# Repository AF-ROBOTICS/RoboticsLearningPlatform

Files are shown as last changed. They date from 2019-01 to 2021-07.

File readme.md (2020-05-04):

# DFEC Robot

The DFEC Robot was created for the Department of Electrical and Computer Engineering (ECE) at the US Air Force Academy. It is used to teach ECE fundamentals in the major's introductory course. The robot's chassis is built using 3D printed parts. An Arduino Uno Rev3 microcontroller board and a custom designed power and motor controller Printed Circuit Board (PCB) are used to control the robot.

## Labs

Six labs guide the students from soldering the PCB and assembling the robot to using distance and line sensors to guide the robot through a maze.

[Robot PCB](Labs/0_robot_pcb/robot_pcb.pdf) - This lab guides students to solder and test their PCB.

[Robot Build](Labs/1_robot_build/robot_build.pdf) - This lab provides instructions to assemble the robot.

[Robot Motors](Labs/2_robot_motors/robot_motors.pdf) - This lab investigates how the Arduino uses Pulse Width Modulation to drive the robot's motors.

[Robot Drive](Labs/3_robot_drive/robot_drive.pdf) - This lab has students control the motors to drive in specified patterns.

[Robot Line Following](Labs/4_robot_linefollowing/robot_linefollowing.pdf) - This lab integrates the Pololu QTR-8RC Line Sensor Array to enable the robot to follow a black line.

[Robot Wall Following](Labs/5_robot_wallfollowing/robot_wallfollowing.pdf) - This lab integrates the Sharp GP2Y051SK0F 2-15 cm Analog Distance Sensor to enable the robot to follow walls.

[Robot Maze](Labs/6_robot_maze/robot_maze.pdf) - This lab is broken up into three parts: 1) follow a line through a maze; 2) follow a line through a maze and turn around and return to the start of the maze; and 3) navigate a walled maze towards a goal location.

## Libraries

There are two custom libraries used to control the robot. These libraries should be copied into library folder at `root/Documents/Arduino/libraries`.

[Motor](Labs/libraries/Motor/Motor.h) - This library provides functions to drive the robot using left and right PWM values (e.g., `Motor_Init()`, `Motor_Forward(int leftDuty, int rightDuty)`, and `Motor_Stop()`)

[QTR-8RC](Labs/libraries/QTR-8RC/QTR-8RC.h) - This library is adapted from the QTRSensors library to utilize the QTR-8RC Reflectance Sensor Array to determine how far the robot is off a line.

## Projects

There are several projects that incorporate the DFEC Robot into different systems. All of these are works in progress and need to be updated to utilize the new libraries.

## Hardware

### 3D Printed Chassis

Frame developed using [AutoDesk Fusion 360](https://www.autodesk.com/products/fusion-360/overview) and printed on a LulzBot Taz 6.

#### [Base layer](3D_Printing/stl/BaseLayer1.stl)

| Top | Bottom |
| :---: | :---: |
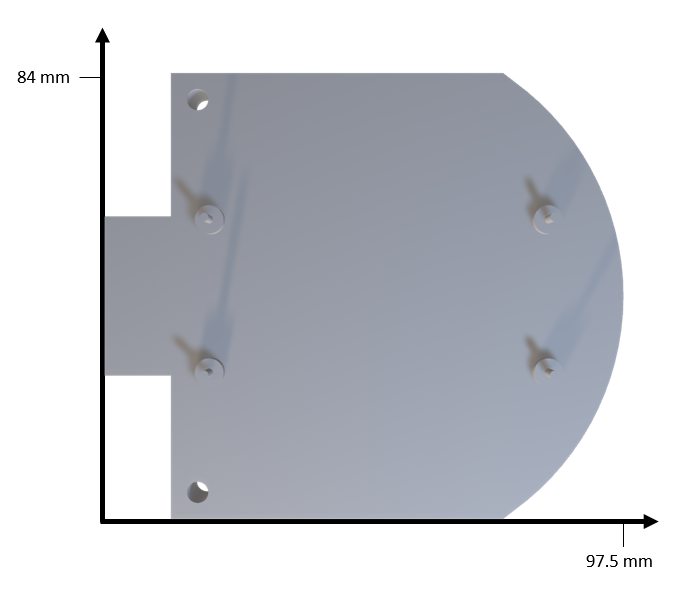
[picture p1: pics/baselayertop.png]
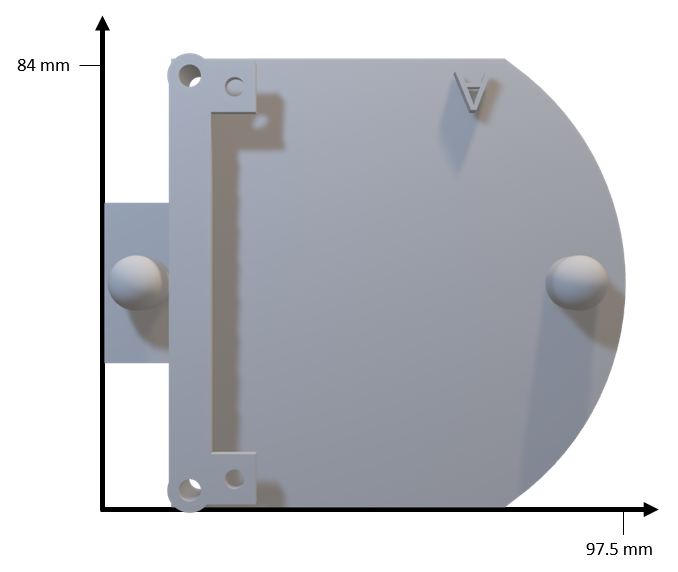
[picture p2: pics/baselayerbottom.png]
|  |  |

#### [Motor layer](3D_Printing/stl/MotorLayer1.stl)

| Top | Bottom |
| :---: | :---: |
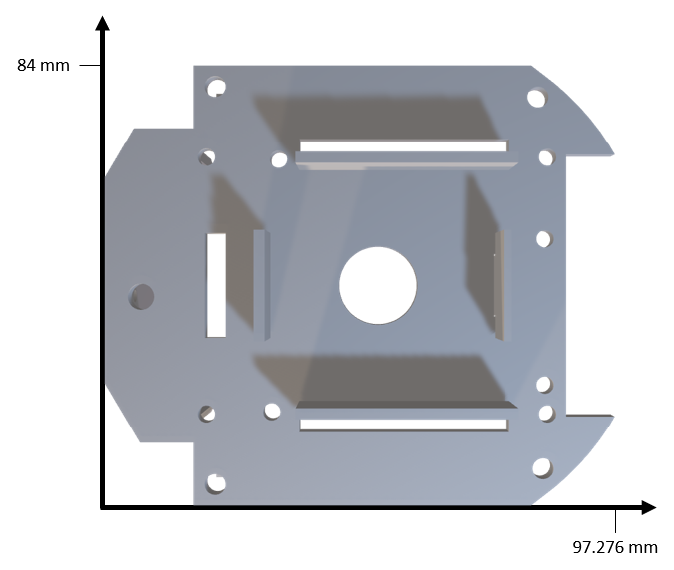
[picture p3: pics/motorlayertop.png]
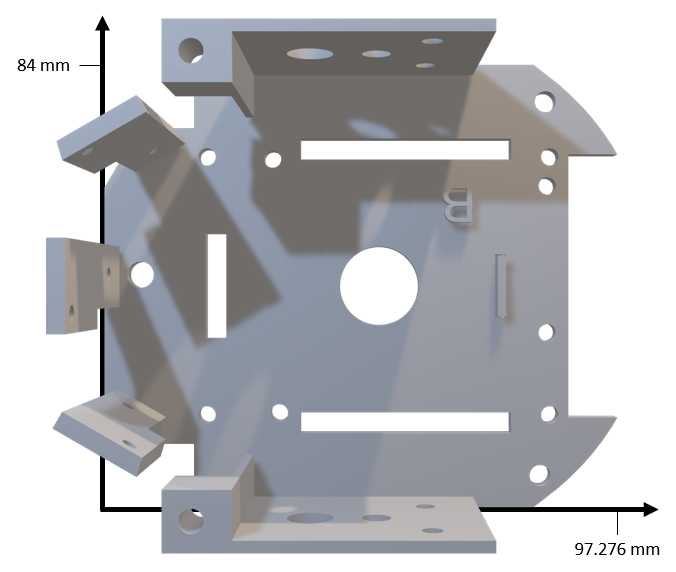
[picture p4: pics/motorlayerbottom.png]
|  |  |

#### [Arduino layer](3D_Printing/stl/ArduinoLayer.stl)

| Top | Bottom |
| :---: | :---: |
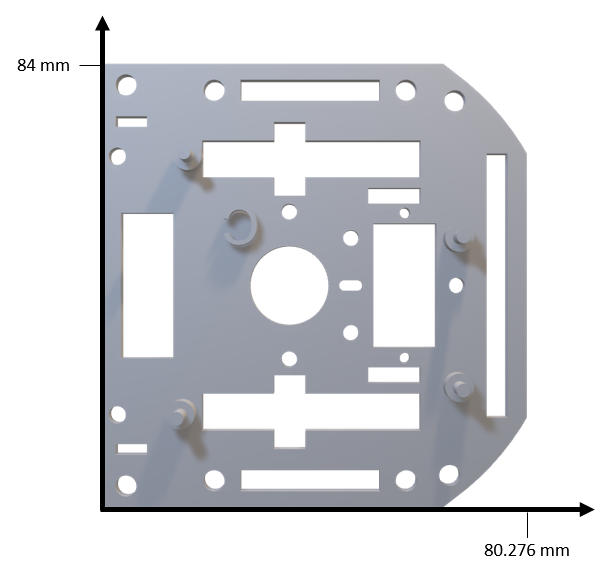
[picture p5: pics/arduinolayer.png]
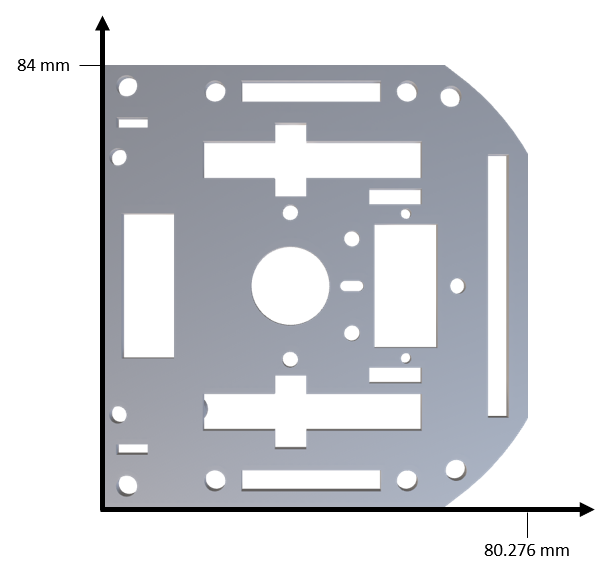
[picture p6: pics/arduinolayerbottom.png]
|  |  |

#### [Additional Layer](3D_Printing/stl/Layer.stl)

| Top | Bottom |
| :---: | :---: |
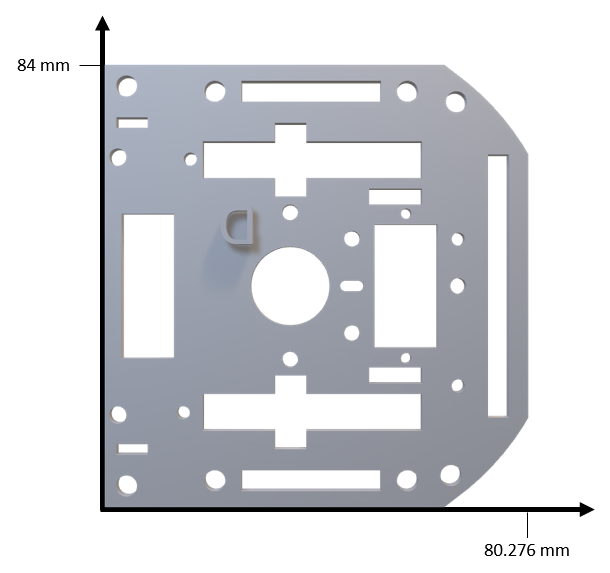
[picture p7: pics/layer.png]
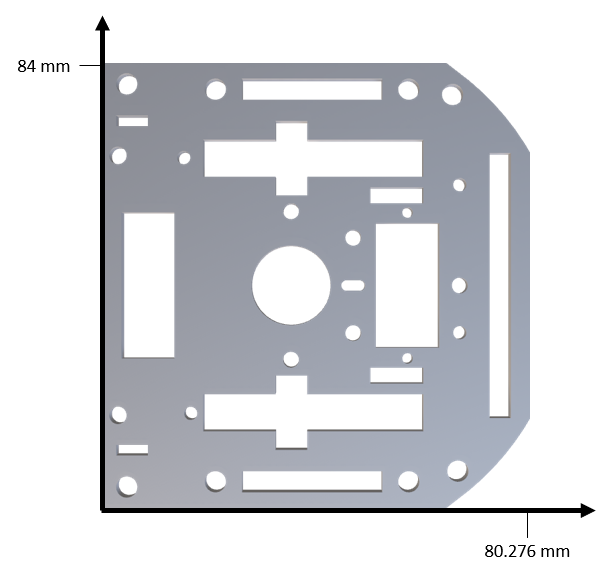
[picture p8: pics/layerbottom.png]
|  |  |

#### Wheels

| [Rims](3D_Printing/stl/rim.STL) | [Tires](3D_Printing/stl/Ninja_Flex_Tire_left.STL) |
| :---: | :---: |
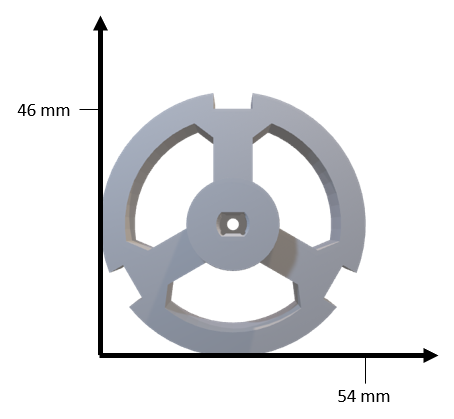
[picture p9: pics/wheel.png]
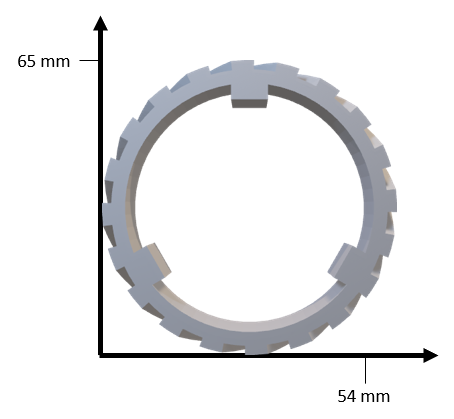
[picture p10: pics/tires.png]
|  |   |

### Printed Circuit Board (PCB)

| | |
| :---: | :---: |
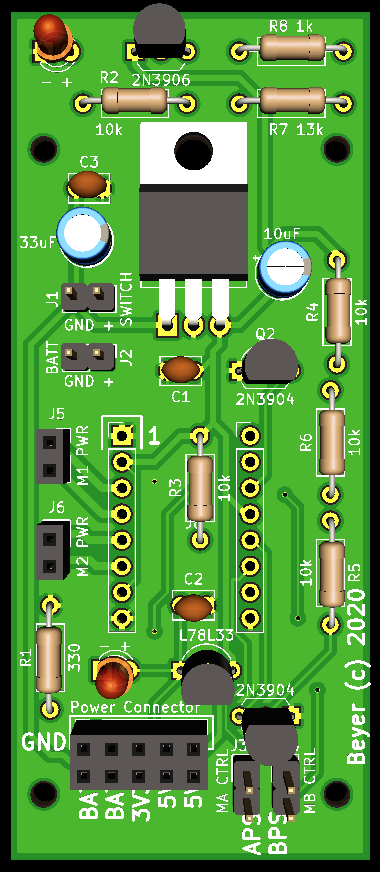
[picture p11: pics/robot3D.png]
|  |  |

### [Motor](https://www.adafruit.com/product/3777)

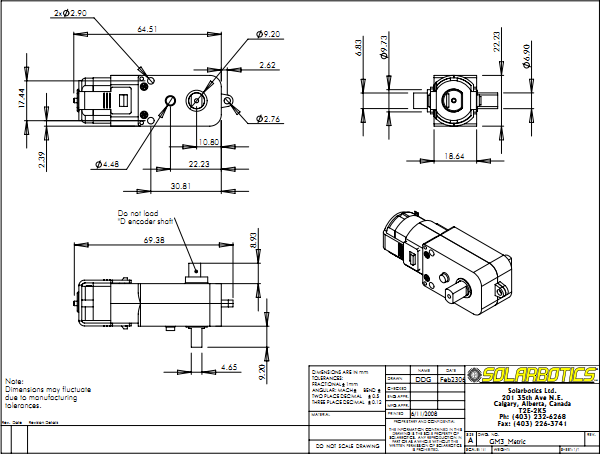
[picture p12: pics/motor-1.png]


### [Sharp GP2Y0A51SK0F Analog Distance Sensor 2-15 cm](https://www.pololu.com/product/2450)

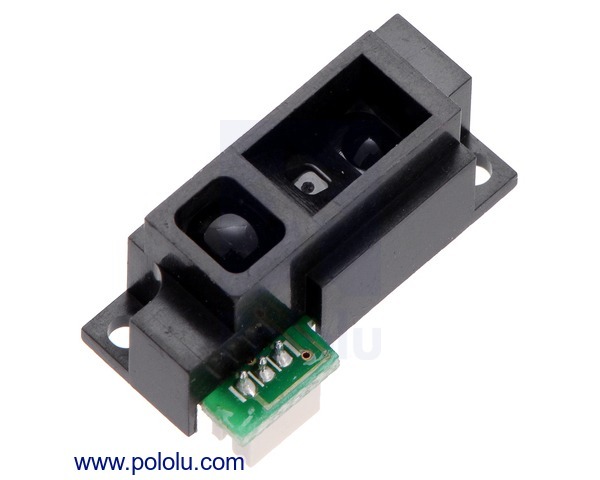
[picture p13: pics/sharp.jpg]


### [QTR-8RC Reflectance Sensor Array](https://www.pololu.com/product/961)

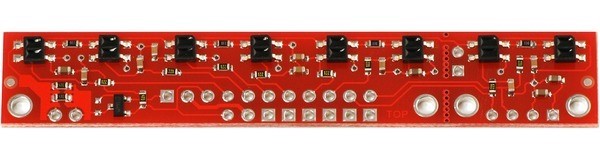
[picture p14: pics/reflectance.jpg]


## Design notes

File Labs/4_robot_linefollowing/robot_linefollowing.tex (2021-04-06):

\documentclass{handout}

%\SetInstructor{Capt Steven Beyer}
\SetCourseTitle{ECE210: Introduction to Electrical and Computer Engineering}
\SetHandoutTitle{Robot Line Following}

%\ShowAllBlanks

\usepackage[obeyspaces]{url}
\input{../arduinoLanguage.tex}

\graphicspath{{./figs/}}

%\showsoln \setsolncolor{red}

\lstset { %
	language=Arduino,
	frame=none,
	basicstyle=\footnotesize,
}

\begin{document}
	\maketitle
		\begin{figure}[H]
		\centering
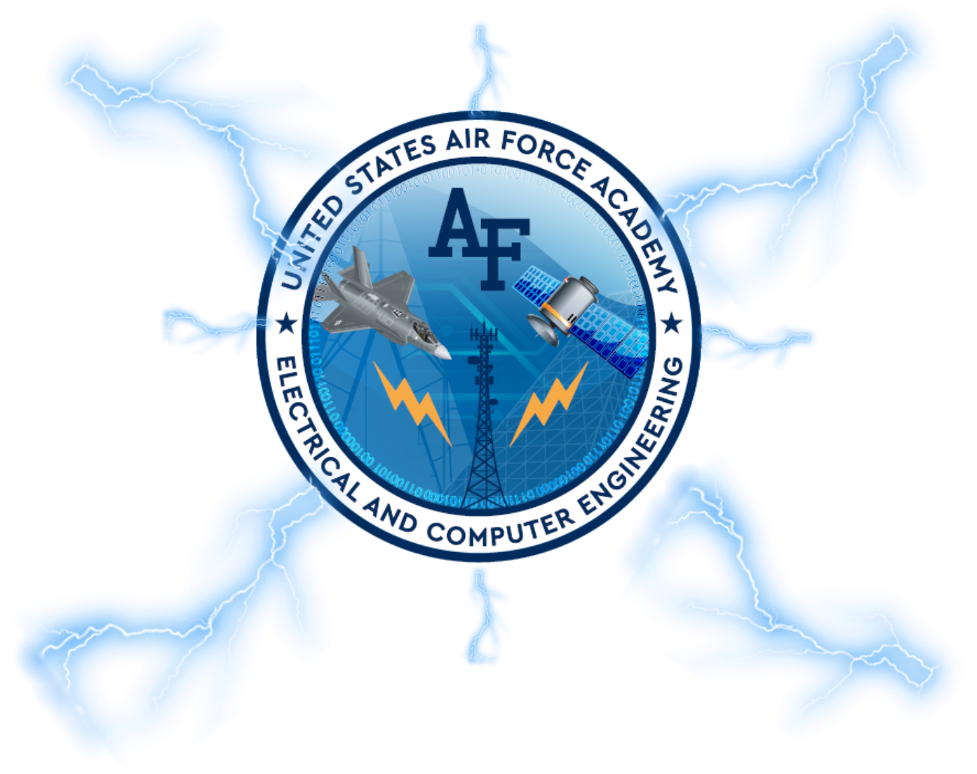
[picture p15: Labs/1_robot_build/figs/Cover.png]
		
	\end{figure}
	
	\section{Objectives.} 
	\begin{enumerate}
		\item Become familiar with the QTR-8RC Line Sensor Array.
		\item Utilize the Arduino to detect lines.
		\item Integrate the Line Sensors with the DFECBot and program the DFECBot to follow a line.
	\end{enumerate}
	
	\section{Materials.}
	\begin{enumerate}
		\item 1x QTR-8RC Reflectance Sensor Array
		\item DFECBot
		\item USB Programming Cable
		\item Black Tape
	\end{enumerate}
	
	\section{Introduction.}
	
	\subsection{QTR-8RC Reflectance Sensor Array}
	The QTR-8RC Line Sensor Array uses 8 infrared radiation (IR) reflectance sensor with an IR light-emitting diode (LED) and an IR sensitive phototransistor.\footnote{Information found at Pololu, \url{https://www.pololu.com/product/961}} The sensors are powered using the $3.3\ V$ and ground pins on the Arduino. Powering the sensors illuminates the IR LED. A $100\ \Omega$ resistor is on-board and placed in series with the LED to limit current. The output of the phototransistor is tied to a $10\ nF$ capacitor. The faster the capacitor discharges, the more reflective the surface is.\footnotemark[1] The QTR sensors have an optimal sensing distance of $3\ mm$.
	
	Wire your QTR-8RC Reflectance Sensor Array to the Arduino according to the schematic shown in Figure~\ref{Fig Line}.
	
	\begin{figure} [H]
		\centering
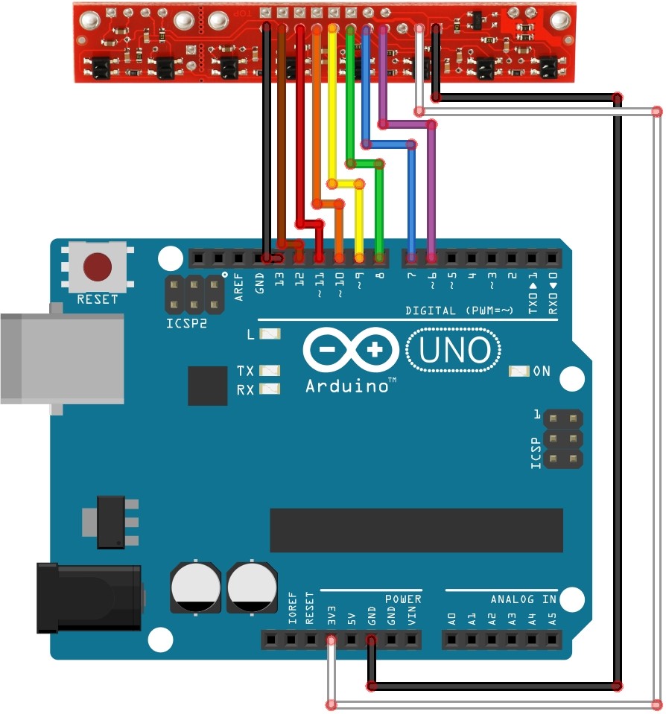
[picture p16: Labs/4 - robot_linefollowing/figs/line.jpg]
		
		\caption{QTR-8RC Reflectance Sensor Array Wiring Schematic}
		\label{Fig Line}
	\end{figure}
	
	\subsection{Example Code}
	Copy the Arduino sketch folder \path{robot_linefollowing}  from \textbf{Teams} (\path{Labs/robot_linefollowing}). Copy the \path{QTR-8RC} library from \textbf{Teams} (\path{Labs/Custom Libraries/QTR-8RC}) to your documents folder: \path{Documents/Arduino/libraries/}. Open the \path{robot_wallfollowing.ino} sketch.
	
	\subsection{QTR-8RC.h}
	The Arduino Sketch utilizes a library called QTR-8RC. This is a custom library adapted from the QTRSensors library to utilize the QTR-8RC Reflectance Sensor Array. This library provides functions to read values from the sensor array and return the distance off the line.
	
	\subsubsection{robot\_linefollowing.ino}
	This example Arduino Sketch provides code to calibrate the DFECBot's QTR-8RC Reflectance Sensor Array and determine the distance off a black line.
	
	\begin{lstlisting}
  // read calibrated sensor values and obtain a measure of the line position
  // with a position of 0.1 mm relative to the center of the line 
  // -33.2 mm to 33.2 mm
  int16_t position = qtr.readLineBlack(sensorValues);
	\end{lstlisting}
	
	\section{Procedure}
	\textbf{Use the example code provided, \path{robot_linefollowing}, \path{Motor.h}, and \path{QTR-8RC.h} to code the DFECBot to do the following:}
		
	\begin{enumerate}
		\item Use a ruler to confirm the accuracy of the line sensor read function
		\item Program the DFECBot to follow a line
	\end{enumerate}
	{\large \textbf{\underline{CALIBRATION:}}} The first 10 seconds after powering on your robot (or uploading the code) is used to calibrate your line sensor. During calibration, \textbf{without lifting your robot off the surface}, slowly move your robot so each line sensor is over a black line for approximately one second. This allows the script to collect minimum (white surface) and maximum (black surface) readings used to calibrate the sensors.
	
	{\large \textbf{\underline{HINT:}}} You should remove all print statements and delays when testing your line following.
	\section{Notes on Proportional Controller:}
\end{document}

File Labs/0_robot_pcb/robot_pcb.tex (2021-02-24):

\documentclass{handout}

%\SetInstructor{Capt Steven Beyer}
\SetCourseTitle{ECE210: Introduction to Electrical and Computer Engineering}
\SetHandoutTitle{Robot PCB}

%\ShowAllBlanks

\usepackage[obeyspaces]{url}

\graphicspath{{./figs/}}

%\showsoln \setsolncolor{red}

\begin{document}
	%	\footnotetext{Examples are abstracted from Tutorials Point, "Arduino", 2019, accessed Feb 18, 2019. [Online]. Available: https://www.tutorialspoint.com/arduino/index.htm}
	\maketitle
	
	\begin{figure}[H]
		\centering
		
	\end{figure}
	
	\section{Objectives.} 
	\begin{enumerate}
		\item Demonstrate the ability to build a robotics system using Electrical and Computer Engineering (ECE) fundamentals such as soldering, assembly, and fabrication.
		\item Troubleshoot ECE applications utilizing modern test equipment.
	\end{enumerate}
	
	\section{Materials.}
\begin{minipage}{.5\textwidth}
	\begin{enumerate}
		\item Printed Circuit Board (PCB)
		\item 1 - $330\ \Omega$ resistor (R1)
		\item 5 - $10\ k\Omega$ resistors (R2 - R6)
		\item 1 - $13\ k\Omega$ resistor (R7)
		\item 1 - $1\ k\Omega$ resistor (R8)
		\item 3 - $0.1\ \mu F$ ceramic disc capacitors (C1-C3)
		\item 1 - $10\ \mu F$ radial capacitor (C4)
		\item 1 - $33\ \mu F$ radial capacitor (C5)
		\item 2 - 2N3904 transistors (Q1-Q2)
		\item 1 - 2N3906 transistor (Q3)
	\end{enumerate}
\end{minipage}\hfill
\begin{minipage}{.5\textwidth}
	\begin{enumerate}\setcounter{enumi}{10}
		\item 1 - L7805 $5\ V$ voltage regulator (U1)
		\item 1 - L78L33 $3.3\ V$ voltage regulator (U2)
		\item 2 - red LEDs
		\item Headers
		\begin{enumerate}
			\item 4 - 1x2 male headers (J1-J4)
			\item 2 - 1x2 female headers (J5 and J6)
			\item 1 - 2x5 female header (Power Connector)
			\item 2 - 8x1 female headers (Motor Driver)
		\end{enumerate}
		\item Motor Driver
		\begin{enumerate}
			\item Motor Driver Board
			\item 2 - 8x1 male headers
		\end{enumerate}
	\end{enumerate}
\end{minipage}

\newpage
\clearpage
\pagebreak
	
	\section{PCB}
	Your PCB should look like the below figure with all components labeled. This PCB provides power and motor functionality for your robot.
		\begin{figure} [H]
			\centering
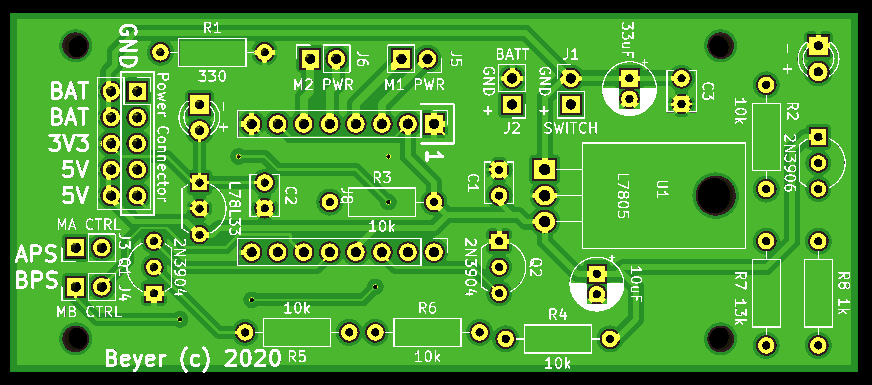
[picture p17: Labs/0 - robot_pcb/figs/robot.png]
			
			\caption{Printed Circuit Board}
		\end{figure}

	\section{Resistors}
	Gather the 8 resistors. Confirm actual resistance using the digital multimeter (DMM). These are non-directional. Solder each onto the board.
	
	\begin{figure} [H]
		\centering
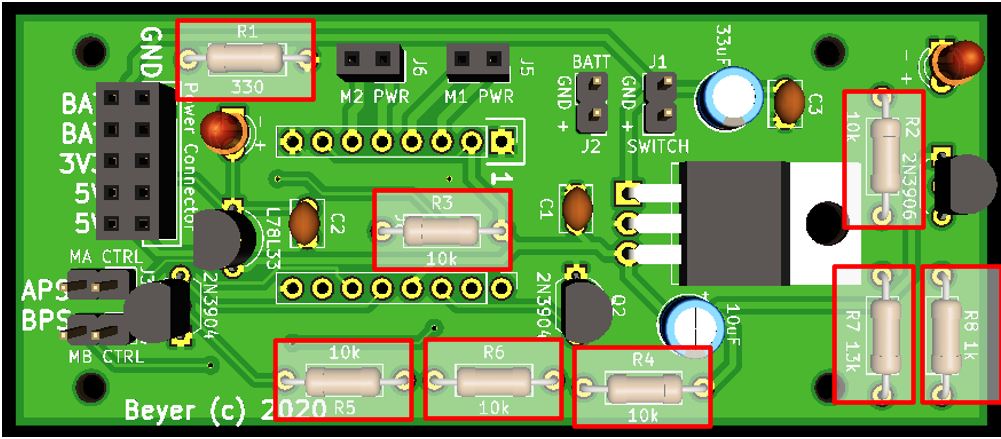
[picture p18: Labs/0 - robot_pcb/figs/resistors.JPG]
		
		\caption{Resistors}
	\end{figure}
	
	\section{Ceramic Disc Capacitors}
	Gather the 3 ceramic disc capacitors. These are non-directional. Solder each onto the board.
	
	\begin{figure} [H]
		\centering
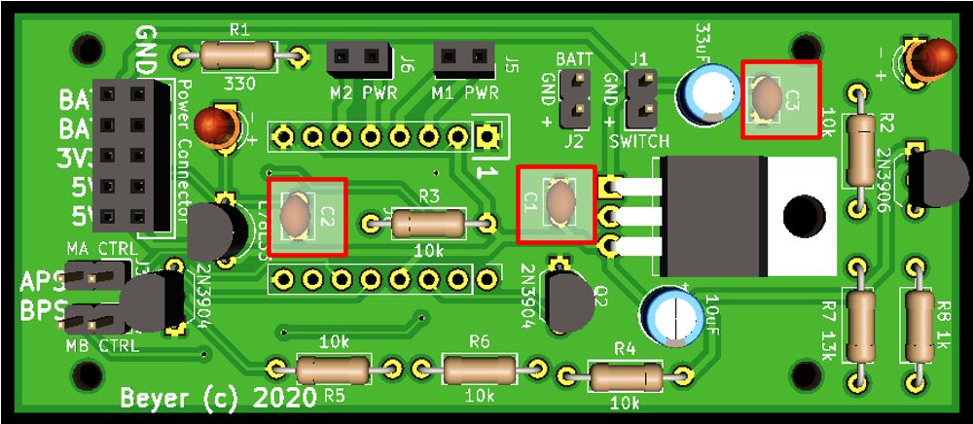
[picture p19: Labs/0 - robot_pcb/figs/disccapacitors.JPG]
		
		\caption{Ceramic Disc Capacitors}
	\end{figure}
	
	\newpage
	\clearpage
	\pagebreak
	
	\section{Radial Capacitors}
	Gather the 2 radial capacitors. These are directional. The negative sign on the capacitor cap should be oriented opposite the positive on the board. Solder each onto the board.
	
	\begin{figure} [H]
	\centering
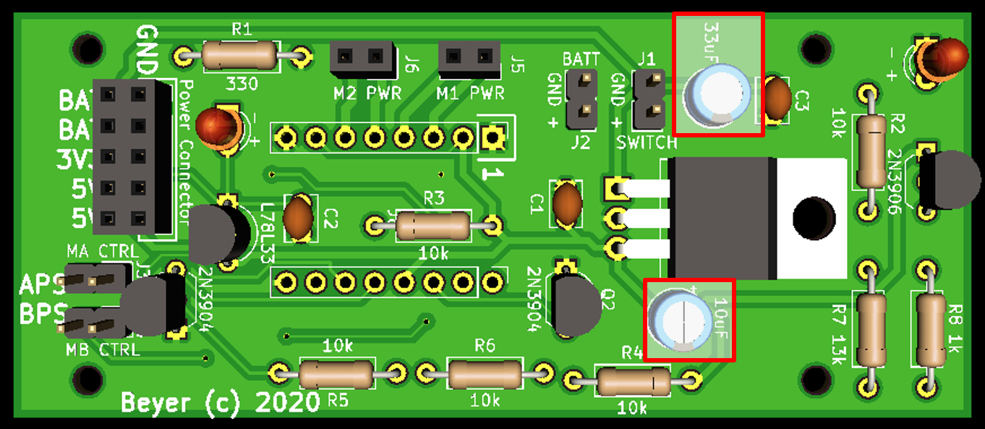
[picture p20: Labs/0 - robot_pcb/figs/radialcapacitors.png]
	
	\caption{Radial Capacitors}
	\end{figure}

	\section{Transistors}
	Gather the 3 transistors. These are directional. The flat edge of the transistor should correspond with the board. Solder each onto the board.
	
	\begin{figure} [H]
		\centering
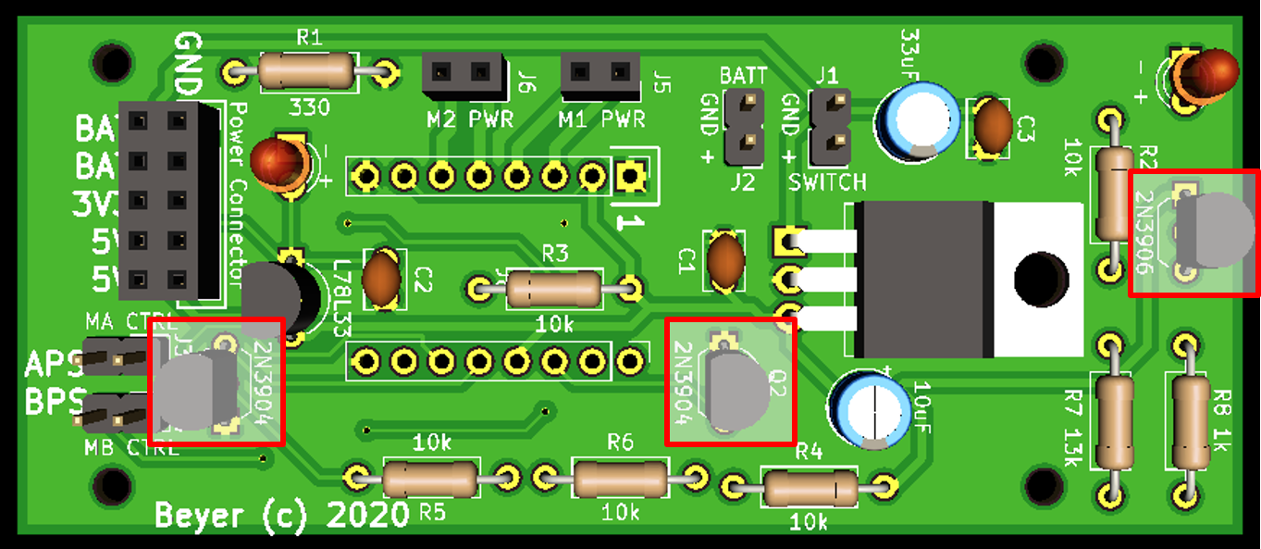
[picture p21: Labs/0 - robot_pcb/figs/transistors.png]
		
		\caption{Transistors}
	\end{figure}
	
	\section{5 V Voltage Regulator}
	Gather the $5\ V$ voltage regulator. Use pliers to bend the leads $90^o$ towards the back of the regulator (flat side) at the point that the lead thins. Place the regulator so that the flat side lays flat on the top of the PCB. Solder it onto the board.
	
	\begin{figure} [H]
		\centering
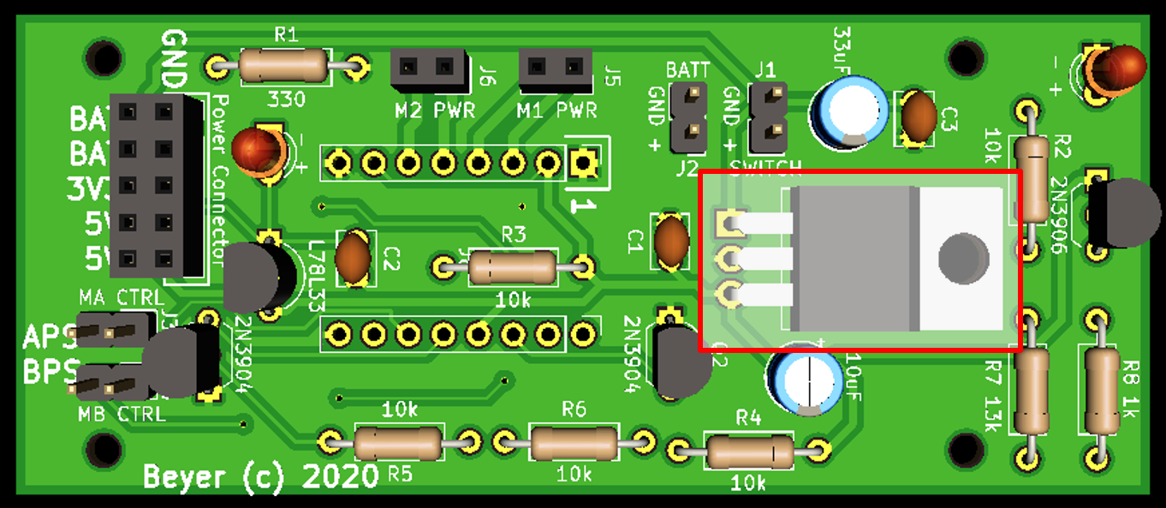
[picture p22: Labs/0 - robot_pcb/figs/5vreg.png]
		
		\caption{$5\ V$ Voltage Regulator}
	\end{figure}

\newpage
\clearpage
\pagebreak

	\section{3.3 V Voltage Regulator}
	Gather the $3.3\ V$ voltage regulator. This is directional. The flat edge of the regulator should correspond with the board. Solder it onto the board.
	
	\begin{figure} [H]
		\centering
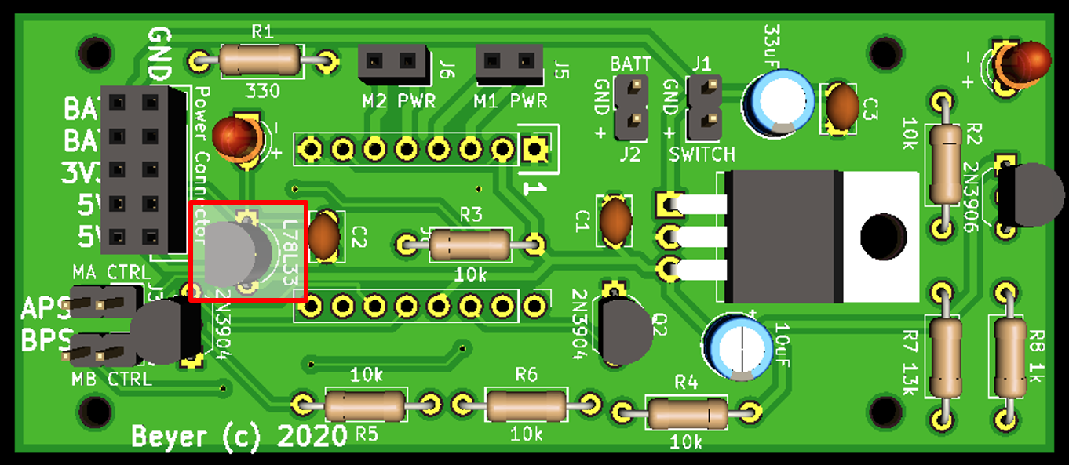
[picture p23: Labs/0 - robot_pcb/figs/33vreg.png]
		
		\caption{$3.3\ V$ Voltage Regulator}
	\end{figure}
	
	\section{LEDs}
	Gather the 2 LEDs. Use the DMM to make sure both are operational. These are directional. The \textbf{flat} edge of the LED and the \textbf{short} lead should be oriented toward the negative on the board. Solder them onto the board.
	
	\begin{figure} [H]
		\centering
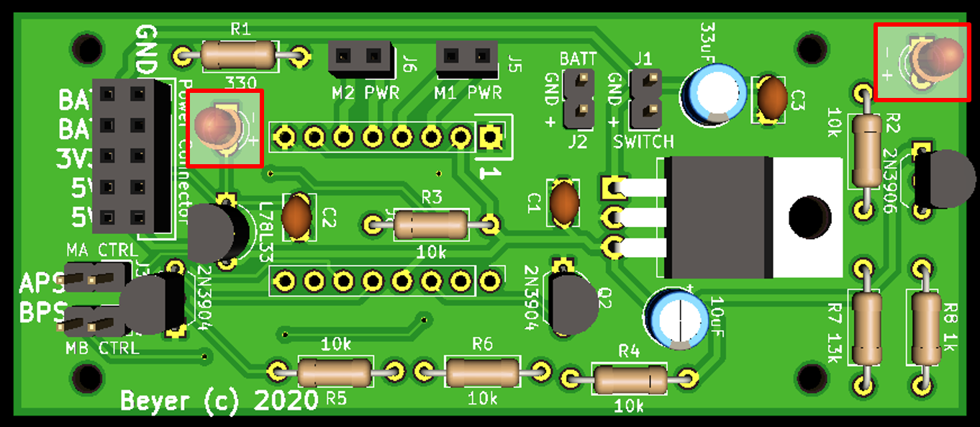
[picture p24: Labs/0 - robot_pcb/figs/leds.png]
		
		\caption{LEDs}
	\end{figure}
	
	\section{Male Headers}
	Gather the 4 - 1x2 male headers. The smaller end of the header should go through the board. Solder them onto the board.
	
	\begin{figure} [H]
		\centering
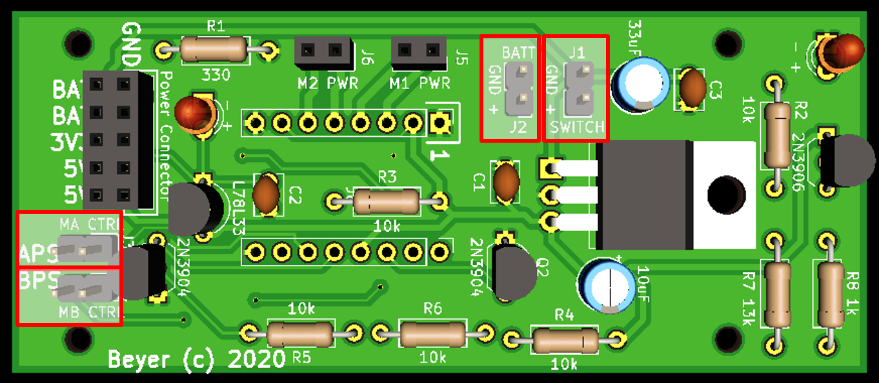
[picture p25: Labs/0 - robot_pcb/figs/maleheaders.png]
		
		\caption{Male Headers}
	\end{figure}

\newpage
\clearpage
\pagebreak

	\section{Female Headers}
	Gather the 5 female headers. Solder them onto the board.
	
	\begin{figure} [H]
		\centering
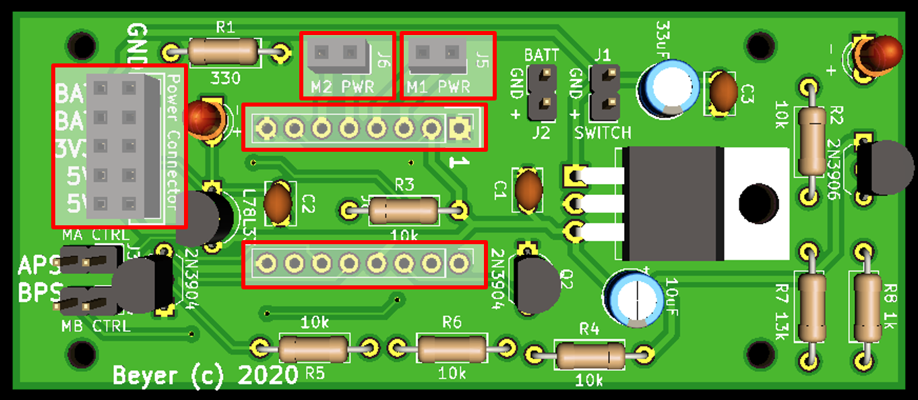
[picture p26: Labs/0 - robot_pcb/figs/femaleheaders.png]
		
		\caption{Female Headers}
	\end{figure}

	\section{PCB with No Motor Driver Board}
	Your board should look like the below figure at this point.
	\begin{figure} [H]
		\centering
		
		\caption{PCB with No Motor Driver Board}
	\end{figure}

	\section{Motor Driver Board}
	Place the long end of the 2 - 1x8 male headers into the 2 female headers. Orient the motor driver board onto the male headers with the in-line capacitor facing the $5\ V$ voltage regulator. Solder the headers onto the motor driver board.
	\begin{figure} [H]
		\centering
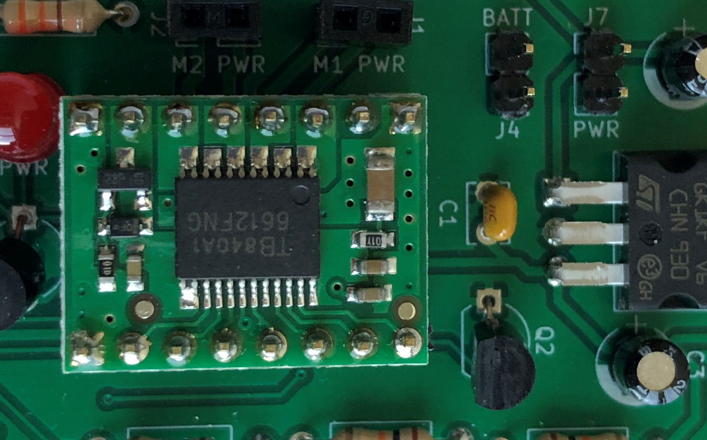
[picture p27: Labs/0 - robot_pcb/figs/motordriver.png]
		
		\caption{Motor Driver Board}
	\end{figure}
	
\newpage
\clearpage
\pagebreak
	
	\section{Completed PCB}
	Your board is now complete and should look like the below figure.
	\begin{figure} [H]
		\centering
		
		\caption{Completed PCB}
	\end{figure}

	\section{Testing the PCB}
	Take your board to the instructor to test that it is operational. The Arduino should use your PCB to drive the motors forward, left, right, and backwards.
	
	\section{Troubleshooting the PCB}
	If your PCB was not operational it is now time to troubleshoot. 
	\begin{enumerate}
		\item Replace your motor driver board with a known operational board from the instructor. Repeat above steps from testing the PCB.
		\item Use the schematics on the next page to test connectivity between components. This will help determine if a solder joint is not making connection with the PCB pad.
	\end{enumerate}

	\begin{figure} [htb]
		\centering
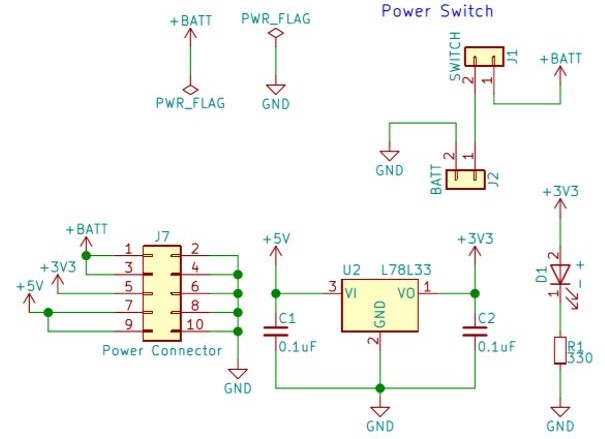
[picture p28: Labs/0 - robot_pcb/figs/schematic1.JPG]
		
		
		\vspace{0cm}
		
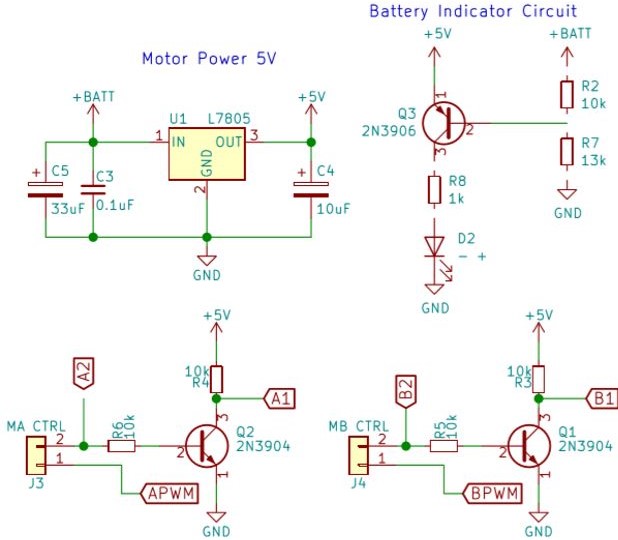
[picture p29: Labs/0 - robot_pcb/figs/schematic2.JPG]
		
		
		\vspace{0cm}
		
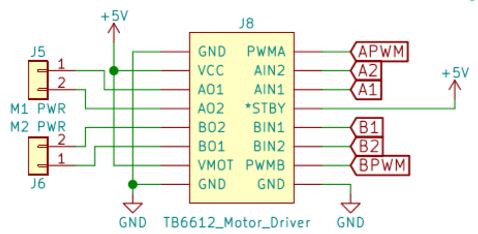
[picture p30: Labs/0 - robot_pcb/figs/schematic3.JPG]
		
	\end{figure}

\end{document}

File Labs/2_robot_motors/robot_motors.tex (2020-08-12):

\documentclass{handout}

%\SetInstructor{Capt Steven Beyer}
\SetCourseTitle{ECE210: Introduction to Electrical and Computer Engineering}
\SetHandoutTitle{Robot Motors}

%\ShowAllBlanks

\usepackage[obeyspaces]{url}
\input{../arduinoLanguage.tex}

\graphicspath{{./figs/}}

%\showsoln \setsolncolor{red}

\lstset { %
	language=Arduino,
	frame=none,
	basicstyle=\footnotesize,
}

\begin{document}
	\maketitle
	\begin{figure}[H]
		\centering
		
	\end{figure}
	
	\section{Objectives.} 
	\begin{enumerate}
		\item Understand the fundamentals of Pulse Width Modulation (PWM) including period, frequency, duty cycle, and pulse width.
		\item Understand how PWM can be used to control the speed of motors.
		\item Demonstrate understanding by manipulating the motors at different speeds.
	\end{enumerate}
	
	\section{Pre-lab - To be done prior of class.}
	\subsection{Reading:}
	Adapted from \underline{Embedded Systems: Real-Time Interfacing to the MSP432 Microcontroller}, Jonathan W. Valvano, Third Edition, 2019.
		
	One effective way to deliver power to a DC motor in a variable manner is to use pulse width modulation (PWM). The basic idea of PWM is to create a \textbf{digital} output wave of fixed frequency, but allow the microctonroller to vary its duty cycle. The system is designed in such a way that \textbf{High+Low} is constant (meaning frequency/period is fixed). The \textbf{duty cycle} is defined as the fraction of time the signal is high:
	
	\[
		duty\ cycle = \frac{High}{High + Low} = \frac{High}{Period}
	\]
	
	Hence, duty cycle varies from 0 to 1 and will often be referred to as a percent. We interface this digital output wave to an external actuator (like a DC motor), such that power is applied to the motor when the signal is high, and no power is applied when the signal is low. We purposely select a frequency high enough so the DC motor does not start/stop with each individual pulse, but rather responds to the overall average value of the wave.
	
	\subsection{Key Terms:}
	\begin{itemize}
		\item \textbf{Pulse Width Modulation (PWM)}: A technique to deliver a variable signal (power) using an on/off signal with a variable percentage of time the signal is on (duty cycle).
		\item \textbf{Period/Frequency}: Time required to complete one full cycle (on/off). Frequency is the inverse of period and is constant. The Arduino pins used by the robot operate at 980 Hz.
		\item \textbf{Duty Cycle}: Percentage of time a digital signal is \textbf{on} over a period of time
	\end{itemize}

	\begin{figure} [H]
	\centering
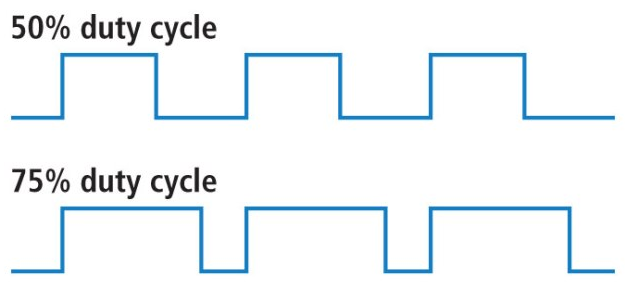
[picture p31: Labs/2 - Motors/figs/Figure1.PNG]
	
\end{figure}	
	
	\subsection{Examples:}
	\begin{enumerate}
		\item Pulsing an LED on and off.

	\begin{minipage}{.4\textwidth}
	You have already applied PWM to pulse the red LED using the Arduino. You varied the duty cycle through the use of the \mbox{\textit{analogWrite()}} function within the \textit{for-loop} which varied the power applied to the LED and consequently, the brightness. The code you used is to the right.
	\end{minipage}\hfill
	\begin{minipage}{.5\textwidth}
	\begin{figure} [H]
		\centering
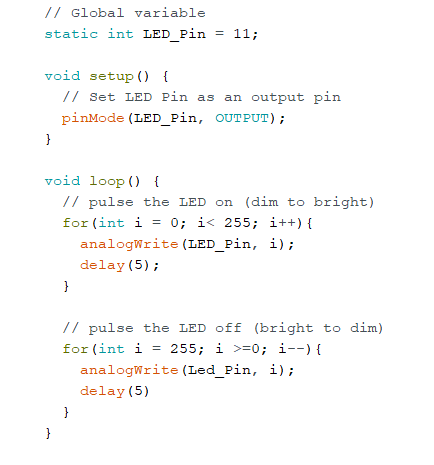
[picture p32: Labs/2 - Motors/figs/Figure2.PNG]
		
	\end{figure}
\end{minipage}
	\newpage
\clearpage
\pagebreak
	\item Answer the following given the example shown below in Figure 1.
\begin{enumerate}
	\item What is the period of the signal?\soln{.2in}{100 ns}
	\item What is the pulse width of the signal (how long is the signal \textbf{HIGH})?\soln{.2in}{25 ns}
	\item What is the duty cycle?\soln{0in}{25\%}
\end{enumerate}

	\begin{figure} [H]
	\centering
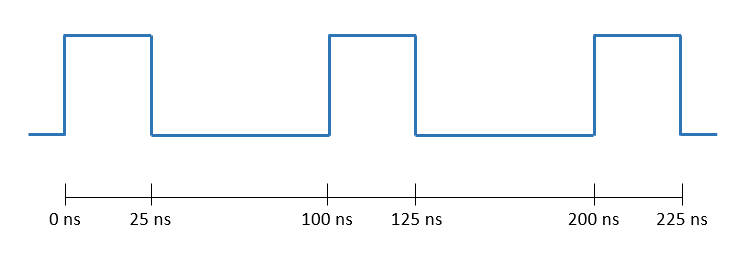
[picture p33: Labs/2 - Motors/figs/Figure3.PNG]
	
	\caption{}
\end{figure}

	\item Given that the \textit{analogWrite(pin, value)} function's \textit{value} parameter is an integer that represents the duty cycle between 0 (always off) and 255 (always on), what would be the \textit{value} passed to provide a 75\% duty cycle to the motors?
	
	\soln{.25in}{$75\% of 255 = 191.25 = 191$}
	
		\end{enumerate}

	\subsection{Code:}
	\begin{enumerate}
		\item Copy the Arduino sketch folder \path{robot_motors} from \textbf{Teams} (\path{Labs/robot_motor})
		\item Open the \path{robot_motors.ino} sketch.
		\item In the \textit{loop()} function, update the five calls to \textit{Motor\_Forward()} to drive the motor at the designated duty cycles. 
		\begin{itemize}
			\item The example provided, \textit{Motor\_Forward(50, 50);}, will drive both the left and right motors at (50/255)\% of the duty cycle. This is equivalent to a duty cycle of about 20\%.
		\end{itemize}
		\item Upload the sketch to the robot. Both motors of the robot should now operate at 6 different speeds (from 20\% duty cycle up to 100\% and back down to 15\%).
	\end{enumerate}
	
	\section{Lab.}
	This lab will demonstrate how varying the PWM signal changes the average power delivered to the DC motors and, effectively, the speed of the motors.
	
	\subsection{Materials:}
	
	\begin{enumerate}
		\item Assembled BeyerBot
		\item Arduino programming cable
		\item Laptop
		\item Male-to-female/male Y-connector and male-to-male wire (provided for you in the Moku:Lab)
	\end{enumerate}

	\subsection{Connect the Moku:Lab probes:}
	\begin{enumerate}
		\item Disconnect \textbf{ONLY} the wire from \textit{Pin-5} on the Arduino.
		\item Insert male end of the Y-connector into \textit{Pin-5}.
		\item Connect the male end of the wire coming from your Printed Circuit Board (the one disconnected from \textit{Pin-5}) into the female end of the Y-connector.
		\item Connect the positive (red) end of the Moku:Lab probe to \textit{Pin-5} on the Arduino using the Y-connector.
		\item Insert a male-to-male wire into the \textit{GND-Pin} on the Arduino and connect the ground (black) end of the Moku:Lab probe to the other end of the wire.
		\item Your setup should now look like Figure 2. All other wires should still be connected as they were previously.
		\begin{figure} [H]
			\centering
			
			\caption{}
		\end{figure}
	\end{enumerate}
			\newpage
	\clearpage
	\pagebreak
	\subsection{Measuring Pulse Width Modulation Signals:}
	\begin{enumerate}
		\item Place your robot on the Digital Multi Meter (DMM) (to allow the program to run without your robot driving away)
		\item Your Moku:Lab display should look like Figure 3. If it does not, raise your hand.
		\begin{figure} [H]
			\centering
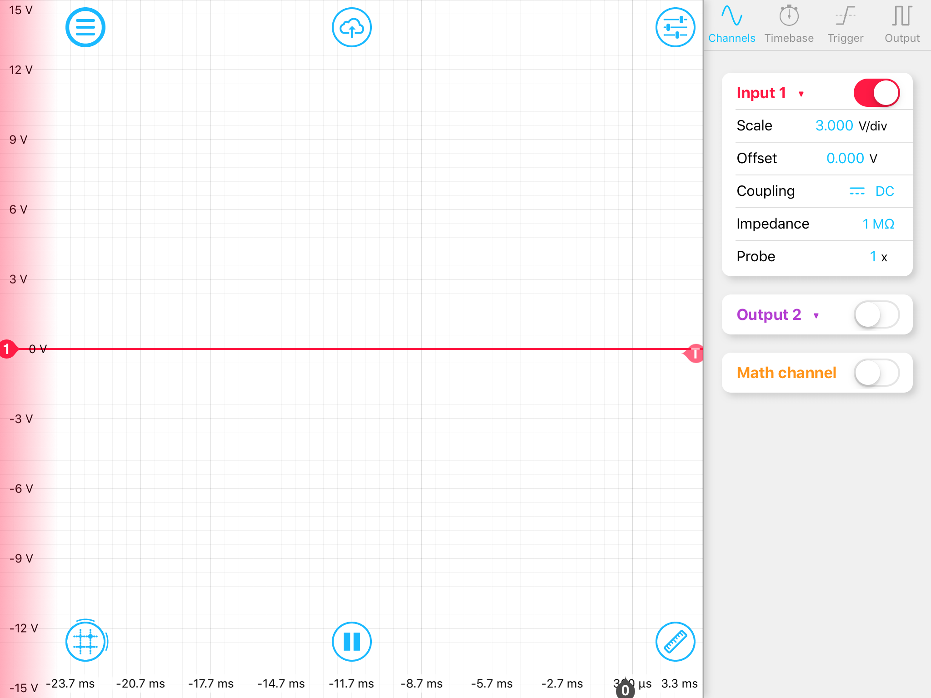
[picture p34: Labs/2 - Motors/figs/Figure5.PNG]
			
			\caption{}
		\end{figure}

		\item Open the measurements bar by pressing the ruler in the bottom right of your screen.
		\begin{figure} [H]
			\centering
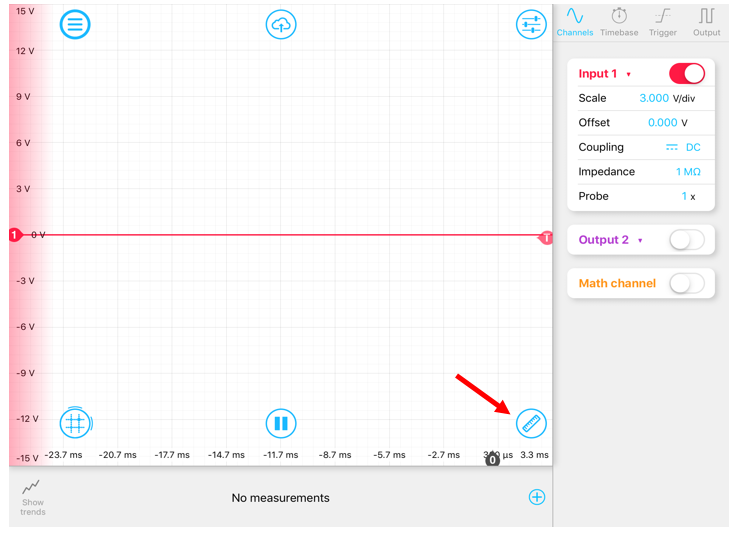
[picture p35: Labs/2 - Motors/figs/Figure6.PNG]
			
		\end{figure}

		\item Add three measurement tools: Frequency, Period, and Pulse width. Press the ``plus" sign within the measurements toolbox to add a new tool. Select the tool to change it. Repeat this for each of the four tools.
		\begin{figure} [H]
			\centering
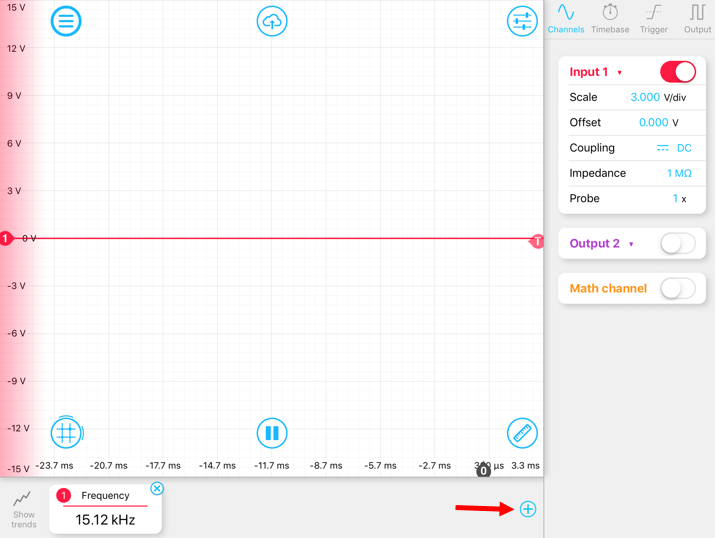
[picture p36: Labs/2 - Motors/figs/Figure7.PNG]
			
		\end{figure}
	\begin{figure} [H]
		\centering
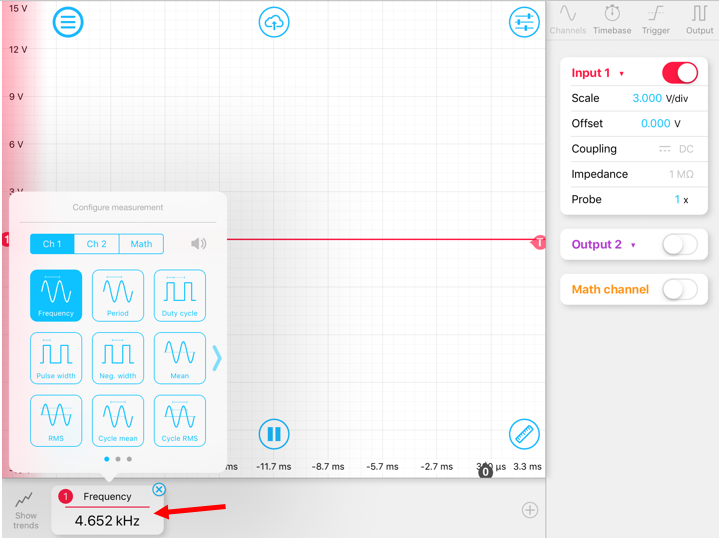
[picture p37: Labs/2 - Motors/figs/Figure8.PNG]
		
	\end{figure}
	\begin{figure} [H]
	\centering
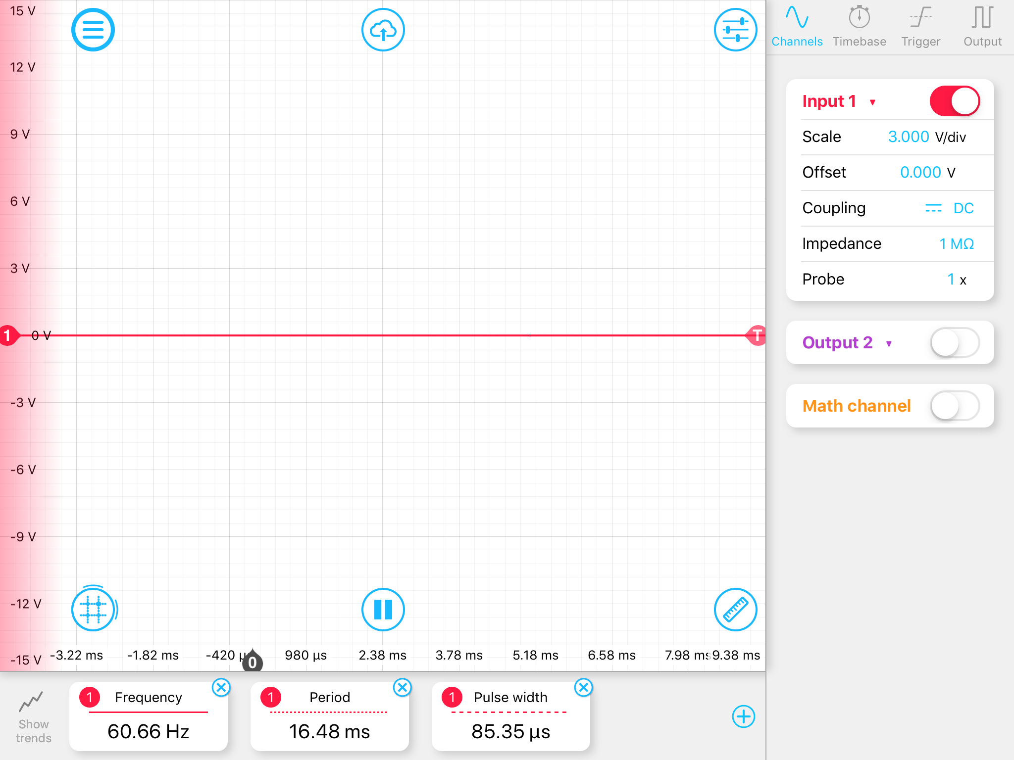
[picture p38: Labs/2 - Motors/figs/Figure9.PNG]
	
\end{figure}
\item Turn on your robot and run the previously uploaded code.
\item What do you notice?

\item Comment out all of the code within \textbf{\textit{loop()}} except for the portion that runs the motors at 75\% duty cycle (\textit{Motor\_Forward(191,191)}; \textit{delay(2000);}) and answer the following questions:
\begin{enumerate}
	\item What is the frequency of the signal? \soln{.3in}{980 Hz}
	\item What is the period of the signal? \soln{.3in}{}
	\item What is the pulse width of the signal (how long is the signal \textbf{HIGH})? \soln{.3in}{}
	\item Using these values, calculate the duty cycle. \soln{.3in}{}
	\item Is this duty cycle what you expected? \soln{.3in}{}
	\item Add a Duty cycle measurement tool on the display (reference step 4.3-4). Does the value match what you calculated?\soln{.3in}{}
	\item How does the speed of the motors correlate to the duty cycle? \soln{.3in}{}
	
\end{enumerate}
	\end{enumerate}
\section{Feedback.}
\begin{enumerate}
	\item Was there any part of the lab that was confusing or unclear? \soln{.3in}{}
	\item Is there any aspect of PWM that you still find confusing or would like more clarification on? \soln{.3in}{}
	\item What would you change from this lab for next semester? \soln{.3in}{}
\end{enumerate}
	
\end{document}

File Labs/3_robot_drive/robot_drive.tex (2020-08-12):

\documentclass{handout}

%\SetInstructor{Capt Steven Beyer}
\SetCourseTitle{ECE210: Introduction to Electrical and Computer Engineering}
%\SetSemester{Spring 2019}
\SetHandoutTitle{Drive Robot}

%\ShowAllBlanks

\usepackage[obeyspaces]{url}
\input{../arduinoLanguage.tex}

%\showsoln \setsolncolor{red}

\graphicspath{{./figs/}}

\lstset { %
	language=Arduino,
	frame=none,
	basicstyle=\footnotesize,
}

\begin{document}
	%	\footnotetext{Examples are abstracted from Tutorials Point, "Arduino", 2019, accessed Feb 18, 2019. [Online]. Available: https://www.tutorialspoint.com/arduino/index.htm}
	\maketitle
	\begin{figure}[H]
	\centering
	
\end{figure}

	\section{Objectives.} 
	\begin{enumerate}
		\item Become familiar with the DFECBot driving functions.
		\item Utilize the Arduino to drive the robot in multiple patterns.
	\end{enumerate}
	
	\section{Materials.}
	\begin{enumerate}
		\item DFECBot
		\item USB Programming Cable
	\end{enumerate}

	\section{Introduction.}
	
	\subsection{Source Files}
	Download the \path{robot_drive} folder from \textbf{Teams} (\path{Labs/drive_robot}). Open \path{robot_drive.ino}. 

	Use Notepad++ to open the \textit{Motor.h} file that you previously saved here:\\ \path{Documents/Arduino/libraries/Motor/Motor.h}. The \textit{.h} file is a header file used within the \textit{.ino}  Arduino sketch. Take a look at \path{Motor.h} first.

	\newpage
\clearpage
\pagebreak	

	\subsubsection{Motor.h}
	This file uses four pins on the Arduino to communicate with the TB6612FNG Motor Driver chip on your PCB board. These pins are used as follows:
	
	\begin{description}
		\item[Pin 2 (L\_DIR)--] Connects to the \textit{APS\_CTRL} pin on the PCB board. This pin sends a signal to the motor driver to control the direction of the left motor.
		
		\item[Pin 3 (L\_PWM) --] Connects to the \textit{APS\_MA} pin on the PCB board. This pin sends a Pulse Width Modulation (PWM) signal to the motor driver to control the speed of left motor.
		
		\item[Pin 4 (R\_DIR)--] Connects to the \textit{BPS\_CTRL} pin on the PCB board. This pin sends a signal to the motor driver to control the direction of the right motor.
		
		\item[Pin 5 (R\_PWM)--] Connects to the \textit{BPS\_MB} pin on the PCB board. This pin sends a Pulse Width Modulation (PWM) signal to the motor driver to control the speed of right motor.
		
	\end{description}
	
	In the \textit{Motor\_Init} function, all four of these pins are set to \textit{OUTPUT} pins. 
	
	The \path{Motor.h} file provides basic drive functions like \textit{Motor\_Forward(leftDuty, rightDuty)} and \textit{Motor\_Stop()}. All movement functions (\textit{Motor\_Forward}, \textit{Motor\_Left}, etc) will run until the next movement function is provided. For example, to get the robot to move forward for 5 seconds then stop, the \textit{Motor\_Forward(leftDuty, rightDuty)} function should be called followed by a 5 second delay and the \textit{Moto\_Stop()} function.
	
	\subsubsection{robot\_drive.ino}
	This is the main file to place drive code. This file is reliant on the \path{Motor.h} header file. The \path{robot\_drive.ino} file provides an example to move the robot forward, turn left, turn right, drive backwards, and then stop. This code will repeat continuously until the DFECBot is powered off (See below code). Delete this example code before submission.

	\begin{lstlisting}
	/* 
	*  Code to make the DFECBot go forward, turn left, turn right, go 
	*  backward and stop. This code will repeat continuously 
	*  until the DFECBot is powered off
	*/
	Motor_Forward(leftDuty, rightDuty);
	delay(2000);
	Motor_Left(leftDuty, rightDuty);
	delay(2000);
	Motor_Right(leftDuty, rightDuty);
	delay(2000);
	Motor_Backward(leftDuty, rightDuty);
	delay(2000);
	Motor_Stop();
	delay(2000);
	\end{lstlisting}

	\section{Procedure}
	\textbf{Use the example code provided and the \path{Motor.h} to code the DFECBot to drive the following patterns. The DFECBot should pause for 2 seconds between each pattern.}
		
	\begin{enumerate}
		\item Drive the DFECBot forward.
		\begin{enumerate}
			\item Drive forward for 5 seconds.
		\end{enumerate}
		\item Drive the DFECBot forward and reverse.
		\begin{enumerate}
			\item Drive forward for 5 seconds.
			\item Pause for 1 second.
			\item Drive in reverse for 5 seconds to return to the starting position.
		\end{enumerate}
		\item Drive the DFECBot forward, turn around, and return to start.
		\begin{enumerate}
			\item Drive forward for 5 seconds.
			\item Pause for 1 second.
			\item Turn around.
			\item Drive back to start and original orientation.
		\end{enumerate}
		\item Drive the DFECBot in a square.
		\begin{enumerate}
			\item Drive in a square making right turns.
			\item Return to the starting location and position.
			\item Drive in a square making left turns.
			\item Return to the starting location and position.
		\end{enumerate}
		\item Drive the DFECBot in a small circle.
		\begin{enumerate}
			\item Drive in a clockwise circle keeping one wheel fixed.
			\item Drive in a counter clockwise circle keeping one wheel fixed.
		\end{enumerate}
		\item Drive the DFECBot in a large circle.
		\begin{enumerate}
			\item Drive in a clockwise circle with an approximate diameter of 2 feet.
			\item Drive in a counter clockwise circle with an approximate diameter of 2 feet.
		\end{enumerate}
		\item Drive the DFECBot in a pattern of choice.
		\begin{enumerate}
			\item Drive in a pattern of your choosing.
		\end{enumerate} 

\end{enumerate}

\end{document}

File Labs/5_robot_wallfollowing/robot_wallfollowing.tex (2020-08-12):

\documentclass{handout}

%\SetInstructor{Capt Steven Beyer}
\SetCourseTitle{ECE210: Introduction to Electrical and Computer Engineering}
\SetSemester{Spring 2019}
\SetHandoutTitle{Robot Wall Following}

%\ShowAllBlanks

\usepackage[obeyspaces]{url}
\input{../arduinoLanguage.tex}

\graphicspath{{./figs/}}

%\showsoln \setsolncolor{red}

\lstset { %
	language=Arduino,
	frame=none,
	basicstyle=\footnotesize,
}

\begin{document}
	%	\footnotetext{Examples are abstracted from Tutorials Point, "Arduino", 2019, accessed Feb 18, 2019. [Online]. Available: https://www.tutorialspoint.com/arduino/index.htm}
	\maketitle
			\begin{figure}[H]
		\centering
		
	\end{figure}
	
	\section{Objectives.} 
	\begin{enumerate}
		\item Become familiar with the Sharp GP2Y0A51SK0F Analog Distance Sensor.
		\item Utilize the Arduino to detect walls.
		\item Integrate the Distance Sensor with the DFECBot and program the DFECBot to avoid obstacles.
	\end{enumerate}
	
	\section{Materials.}
	\begin{enumerate}
		\item 3x Sharp GP2Y0A51SK0F Analog Distance Sensor
		\item USB Programming Cable
		\item DFECBot
	\end{enumerate}

	\newpage
\clearpage
\pagebreak
	
	\section{Introduction.}
	
	\subsection{Sharp GP2Y0A51SK0F Analog Distance Sensor}
	The Sharp GP2Y0A51SK0F Analog Distance Sensor uses an infrared radiation (IR) reflectance sensor with an IR light-emitting diode (LED) and an IR sensitive phototransistor.\footnote{GP2Y0A51SK0F Datasheet, \url{https://www.pololu.com/file/0J845/GP2Y0A41SK0F.pdf.pdf}}Ensure your three sensors are wired per the below diagram.
	
	\begin{figure} [H]
		\centering
		
		\caption{Sharp GP2Y0A51SK0F Analog Distance Sensor Wiring Schematic}
		\label{Fig IR}
	\end{figure}

	\subsection{Example Code}
	Copy the Arduino sketch folder \path{robot_wallfollowing}  from \textbf{Teams} (\path{Labs/robot_wallfollowing}). Open the \path{robot_wallfollowing.ino} sketch.
	
	\subsubsection{SharpDistanceSensor.h}
	The Arduino Sketch utilizes a library called SharpDistSensor. This library provides functions to read values from the Sharp IR sensors. You need to install this library for the example code to work.
	\begin{enumerate}
		\item Click \textit{Tools} $\rightarrow$ \textit{Manage Libraries}
		\item Search for SharpDistSensor
		\item Select Install
	\end{enumerate}
	
	\subsubsection{robot\_wallfollowing.ino}
	This example Arduino Sketch provides code to read the values from the DFECBot's right Distance Sensor (see below example) and provides a distance value in $mm$.
	
	\begin{lstlisting}
		// Read distance (in mm) for each sensor
		unsigned int distR = sensorR.getDist() + OFFSET;
		Serial.print("Right: "); Serial.println(distR);
	\end{lstlisting}
	
	\section{Procedure}
	\textbf{Use the example code provided to code the DFECBot to do the following:}
		
	\begin{enumerate}
		\item Print the values from the DFECBot's center and left GP2Y0A51SK0F Analog Distance Sensor to the serial monitor.
		\item Use a ruler to confirm the accuracy of each distance sensor - the sensor should be fairly accurate between $3\ cm$ and $12\ cm$.
		\item Program the DFECBot to follow wall on right.
		\item Program the DFECBot to follow wall on left.
		\item Program the DFECBot to stay between two walls.
	\end{enumerate} 	
	{\large \textbf{\underline{HINT:}}} You should remove all print statements and delays when testing your wall following.
	\section{Notes on Proportional Controller:}
	
\end{document}

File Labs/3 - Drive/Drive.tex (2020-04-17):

\documentclass{handout}

%\SetInstructor{Capt Steven Beyer}
\SetCourseTitle{ECE210: Introduction to Electrical and Computer Engineering}
%\SetSemester{Spring 2019}
\SetHandoutTitle{Driving the BeyerBot}

%\ShowAllBlanks

\usepackage[obeyspaces]{url}
\input{../arduinoLanguage.tex}

%\showsoln \setsolncolor{red}

\lstset { %
	language=Arduino,
	frame=none,
	basicstyle=\footnotesize,
}

\begin{document}
	%	\footnotetext{Examples are abstracted from Tutorials Point, "Arduino", 2019, accessed Feb 18, 2019. [Online]. Available: https://www.tutorialspoint.com/arduino/index.htm}
	\maketitle

	\section{Objectives.} 
	\begin{enumerate}
		\item Become familiar with the DFECBot driving functions.
		\item Utilize the Arduino to drive the robot in multiple patterns.
	\end{enumerate}
	
	\section{Materials.}
	\begin{enumerate}
		\item DFECBot
		\item USB Programming Cable
	\end{enumerate}
	
	\newpage
	\clearpage
	\pagebreak
	
	\section{Introduction.}
	
	\subsection{Source Files}
	Browse to \path{K:\DF\DFEC\ECE210\Labs\Lab 9 - Driving the Robot} and copy the \path{robot_drive} folder to your computer. Open \path{robot_drive.ino}. 

	Use Notepad++ to open the \textit{Motor.h} file that you previously saved here: \path{Program Files (x86)/Arduino/libraries/Motor/Motor.h}. The \textit{.h} file is a header file used within the \textit{.ino}  Arduino sketch. Take a look at \path{Motor.h} first.
	
	\subsubsection{Motor.h}
	This file uses four pins on the Arduino to communicate with the TB6612FNG Motor Driver chip on your PCB board. These pins are used as follows:
	
	\begin{description}
		\item[Pin 4 (L\_DIR)--] Connects to the \textit{APS\_CTRL} pin on the PCB board. This pin sends a signal to the motor driver to control the direction of the left motor.
		
		\item[Pin 5 (L\_PWM) --] Connects to the \textit{APS\_MA} pin on the PCB board. This pin sends a Pulse Width Modulation (PWM) signal to the motor driver to control the speed of left motor.
		
		\item[Pin 6 (R\_PWM)--] Connects to the \textit{BPS\_MB} pin on the PCB board. This pin sends a Pulse Width Modulation (PWM) signal to the motor driver to control the speed of right motor.
		\item[Pin 7 (R\_DIR)--] Connects to the \textit{BPS\_CTRL} pin on the PCB board. This pin sends a signal to the motor driver to control the direction of the right motor.
	\end{description}
	
	In the \textit{Motor\_Init} function, all four of these pins are set to \textit{OUTPUT} pins. 
	
	The \path{Motor.h} file provides basic drive functions like \textit{Motor\_Forward(leftDuty, rightDuty)} and \textit{Motor\_Stop()}. All movement functions (\textit{Motor\_Forward}, \textit{Motor\_Left}, etc) will run until the next movement function is provided. For example, to get the robot to move forward for 5 seconds then stop, the \textit{Motor\_Forward(leftDuty, rightDuty)} function should be called followed by a 5 second delay and the \textit{Moto\_Stop()} function.
	
	\subsubsection{robot\_drive.ino}
	This is the main file to place drive code. This file is reliant on the \path{Motor.h} header file. The \path{robot\_drive.ino} file provides an example to move the robot forward, turn left, turn right, drive backwards, and then stop. This code will repeat continuously until the DFECBot is powered off (See below code). Delete this example code before submission.
	
	\begin{lstlisting}
	/* 
	*  Code to make the DFECBot go forward, turn left, turn right, go 
	*  backward and stop. This code will repeat continuously 
	*  until the DFECBot is powered off
	*/
	Motor_Forward(leftDuty, rightDuty);
	delay(2000);
	Motor_Left(leftDuty, rightDuty);
	delay(2000);
	Motor_Right(leftDuty, rightDuty);
	delay(2000);
	Motor_Backward(leftDuty, rightDuty);
	delay(2000);
	Motor_Stop();
	delay(2000);
	\end{lstlisting}
	
	\newpage
	\clearpage
	\pagebreak
	
	\section{Procedure}
	\textbf{Use the example code provided and the \path{Motor.h} to code the DFECBot to drive the following patterns. The DFECBot should pause for 2 seconds between each pattern.}
		
	\begin{enumerate}
		\item Drive the DFECBot forward.
		\begin{enumerate}
			\item Drive forward for 5 seconds.
		\end{enumerate}
		\item Drive the DFECBot forward and reverse.
		\begin{enumerate}
			\item Drive forward for 5 seconds.
			\item Pause for 1 second.
			\item Drive in reverse for 5 seconds to return to the starting position.
		\end{enumerate}
		\item Drive the DFECBot forward, turn around, and return to start.
		\begin{enumerate}
			\item Drive forward for 5 seconds.
			\item Pause for 1 second.
			\item Turn around.
			\item Drive back to start and original orientation.
		\end{enumerate}
		\item Drive the DFECBot in a square.
		\begin{enumerate}
			\item Drive in a square making right turns.
			\item Return to the starting location and position.
			\item Drive in a square making left turns.
			\item Return to the starting location and position.
		\end{enumerate}
		\item Drive the DFECBot in a small circle.
		\begin{enumerate}
			\item Drive in a clockwise circle keeping one wheel fixed.
			\item Drive in a counter clockwise circle keeping one wheel fixed.
		\end{enumerate}
		\item Drive the DFECBot in a large circle.
		\begin{enumerate}
			\item Drive in a clockwise circle with an approximate diameter of 2 feet.
			\item Drive in a counter clockwise circle with an approximate diameter of 2 feet.
		\end{enumerate}
		\item Drive the DFECBot in a pattern of choice.
		\begin{enumerate}
			\item Drive in a pattern of your choosing.
		\end{enumerate} 

\end{enumerate}

\end{document}

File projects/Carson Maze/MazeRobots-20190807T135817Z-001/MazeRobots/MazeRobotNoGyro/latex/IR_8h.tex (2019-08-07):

\hypertarget{IR_8h}{}\section{P\+C\+B\+\_\+test/\+P\+C\+B\+\_\+test/\+IR.h File Reference}
\label{IR_8h}\index{P\+C\+B\+\_\+test/\+P\+C\+B\+\_\+test/\+I\+R.\+h@{P\+C\+B\+\_\+test/\+P\+C\+B\+\_\+test/\+I\+R.\+h}}

Contains the \hyperlink{classIRSensor}{I\+R\+Sensor} class, for making IR sensor use easier.  

This graph shows which files directly or indirectly include this file\+:
\nopagebreak
\begin{figure}[H]
\begin{center}
\leavevmode

\end{center}
\end{figure}
\subsection*{Classes}
\begin{DoxyCompactItemize}
\item 
class \hyperlink{classIRSensor}{I\+R\+Sensor}
\begin{DoxyCompactList}\small\item\em Allows for accessing the distance measurements of an IR sensor. \end{DoxyCompactList}\end{DoxyCompactItemize}
\subsection*{Variables}
\begin{DoxyCompactItemize}
\item 
\mbox{\Hypertarget{IR_8h_a58a08a86c9319aacf2a6f4f384a9a6a7}\label{IR_8h_a58a08a86c9319aacf2a6f4f384a9a6a7}} 
constexpr const size\+\_\+t {\bfseries I\+R\+\_\+samples} = 100
\end{DoxyCompactItemize}

\subsection{Detailed Description}
Contains the \hyperlink{classIRSensor}{I\+R\+Sensor} class, for making IR sensor use easier.

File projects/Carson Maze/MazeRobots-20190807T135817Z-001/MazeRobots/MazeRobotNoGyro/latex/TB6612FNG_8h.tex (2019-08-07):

\hypertarget{TB6612FNG_8h}{}\section{P\+C\+B\+\_\+test/\+P\+C\+B\+\_\+test/\+T\+B6612\+F\+NG.h File Reference}
\label{TB6612FNG_8h}\index{P\+C\+B\+\_\+test/\+P\+C\+B\+\_\+test/\+T\+B6612\+F\+N\+G.\+h@{P\+C\+B\+\_\+test/\+P\+C\+B\+\_\+test/\+T\+B6612\+F\+N\+G.\+h}}

Contains a low-\/level control interface for the motor driver chip.  

This graph shows which files directly or indirectly include this file\+:
\nopagebreak
\begin{figure}[H]
\begin{center}
\leavevmode

\end{center}
\end{figure}
\subsection*{Classes}
\begin{DoxyCompactItemize}
\item 
class \hyperlink{classMotorDriver}{Motor\+Driver}
\end{DoxyCompactItemize}
\subsection*{Variables}
\begin{DoxyCompactItemize}
\item 
const int \hyperlink{TB6612FNG_8h_a059bd507e81f5c1acf31887a06c61abd}{Rdir} = 4
\item 
\mbox{\Hypertarget{TB6612FNG_8h_af31057357531366da095242d79844028}\label{TB6612FNG_8h_af31057357531366da095242d79844028}} 
const int {\bfseries pwmR} = 6
\item 
\mbox{\Hypertarget{TB6612FNG_8h_ab4b58100911d5e2635258d949826ed2a}\label{TB6612FNG_8h_ab4b58100911d5e2635258d949826ed2a}} 
const int {\bfseries Ldir} = 9
\item 
\mbox{\Hypertarget{TB6612FNG_8h_a1fbf61284e18275b946866831c7efb94}\label{TB6612FNG_8h_a1fbf61284e18275b946866831c7efb94}} 
const int {\bfseries pwmL} = 5
\end{DoxyCompactItemize}

\subsection{Detailed Description}
Contains a low-\/level control interface for the motor driver chip. 

\subsection{Variable Documentation}
\mbox{\Hypertarget{TB6612FNG_8h_a059bd507e81f5c1acf31887a06c61abd}\label{TB6612FNG_8h_a059bd507e81f5c1acf31887a06c61abd}} 
\index{T\+B6612\+F\+N\+G.\+h@{T\+B6612\+F\+N\+G.\+h}!Rdir@{Rdir}}
\index{Rdir@{Rdir}!T\+B6612\+F\+N\+G.\+h@{T\+B6612\+F\+N\+G.\+h}}
\subsubsection{\texorpdfstring{Rdir}{Rdir}}
{\footnotesize\ttfamily const int Rdir = 4}

A\+Tmega328P, pwm works on pins 3, 5, 6, 9, 10, and 11 at 490/980\+Hz

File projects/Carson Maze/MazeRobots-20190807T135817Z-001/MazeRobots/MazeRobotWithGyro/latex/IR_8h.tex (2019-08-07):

\hypertarget{IR_8h}{}\section{P\+C\+B\+\_\+test/\+P\+C\+B\+\_\+test/\+IR.h File Reference}
\label{IR_8h}\index{P\+C\+B\+\_\+test/\+P\+C\+B\+\_\+test/\+I\+R.\+h@{P\+C\+B\+\_\+test/\+P\+C\+B\+\_\+test/\+I\+R.\+h}}

Contains the \hyperlink{classIRSensor}{I\+R\+Sensor} class, for making IR sensor use easier.  

This graph shows which files directly or indirectly include this file\+:\nopagebreak
\begin{figure}[H]
\begin{center}
\leavevmode

\end{center}
\end{figure}
\subsection*{Classes}
\begin{DoxyCompactItemize}
\item 
class \hyperlink{classIRSensor}{I\+R\+Sensor}
\begin{DoxyCompactList}\small\item\em Allows for accessing the distance measurements of an IR sensor. \end{DoxyCompactList}\end{DoxyCompactItemize}
\subsection*{Variables}
\begin{DoxyCompactItemize}
\item 
\mbox{\Hypertarget{IR_8h_a58a08a86c9319aacf2a6f4f384a9a6a7}\label{IR_8h_a58a08a86c9319aacf2a6f4f384a9a6a7}} 
constexpr const size\+\_\+t {\bfseries I\+R\+\_\+samples} = 100
\end{DoxyCompactItemize}

\subsection{Detailed Description}
Contains the \hyperlink{classIRSensor}{I\+R\+Sensor} class, for making IR sensor use easier.

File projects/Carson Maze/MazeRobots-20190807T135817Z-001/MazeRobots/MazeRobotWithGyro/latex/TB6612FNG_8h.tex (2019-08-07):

\hypertarget{TB6612FNG_8h}{}\section{P\+C\+B\+\_\+test/\+P\+C\+B\+\_\+test/\+T\+B6612\+F\+NG.h File Reference}
\label{TB6612FNG_8h}\index{P\+C\+B\+\_\+test/\+P\+C\+B\+\_\+test/\+T\+B6612\+F\+N\+G.\+h@{P\+C\+B\+\_\+test/\+P\+C\+B\+\_\+test/\+T\+B6612\+F\+N\+G.\+h}}

Contains a low-\/level control interface for the motor driver chip.  

This graph shows which files directly or indirectly include this file\+:\nopagebreak
\begin{figure}[H]
\begin{center}
\leavevmode

\end{center}
\end{figure}
\subsection*{Classes}
\begin{DoxyCompactItemize}
\item 
class \hyperlink{classMotorDriver}{Motor\+Driver}
\end{DoxyCompactItemize}
\subsection*{Variables}
\begin{DoxyCompactItemize}
\item 
const int \hyperlink{TB6612FNG_8h_a059bd507e81f5c1acf31887a06c61abd}{Rdir} = 4
\item 
\mbox{\Hypertarget{TB6612FNG_8h_af31057357531366da095242d79844028}\label{TB6612FNG_8h_af31057357531366da095242d79844028}} 
const int {\bfseries pwmR} = 6
\item 
\mbox{\Hypertarget{TB6612FNG_8h_ab4b58100911d5e2635258d949826ed2a}\label{TB6612FNG_8h_ab4b58100911d5e2635258d949826ed2a}} 
const int {\bfseries Ldir} = 9
\item 
\mbox{\Hypertarget{TB6612FNG_8h_a1fbf61284e18275b946866831c7efb94}\label{TB6612FNG_8h_a1fbf61284e18275b946866831c7efb94}} 
const int {\bfseries pwmL} = 5
\end{DoxyCompactItemize}

\subsection{Detailed Description}
Contains a low-\/level control interface for the motor driver chip. 

\subsection{Variable Documentation}
\mbox{\Hypertarget{TB6612FNG_8h_a059bd507e81f5c1acf31887a06c61abd}\label{TB6612FNG_8h_a059bd507e81f5c1acf31887a06c61abd}} 
\index{T\+B6612\+F\+N\+G.\+h@{T\+B6612\+F\+N\+G.\+h}!Rdir@{Rdir}}
\index{Rdir@{Rdir}!T\+B6612\+F\+N\+G.\+h@{T\+B6612\+F\+N\+G.\+h}}
\subsubsection{\texorpdfstring{Rdir}{Rdir}}
{\footnotesize\ttfamily const int Rdir = 4}

A\+Tmega328P, pwm works on pins 3, 5, 6, 9, 10, and 11 at 490/980\+Hz

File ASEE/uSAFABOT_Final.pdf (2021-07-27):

µSAFABOT: A Robotics Learning Platform for a Hands-On Laboratory Based Approach in an Introductory ECE Course

Abstract
This paper focuses on the design, implementation, and evaluation of an introductory electrical and computer engineering course that integrates theory, hands-on practice, and real-world application through the implementation of a fully customizable robotics system, µSAFABOT. This course is required for all electrical and computer engineering students, but specifically targets undeclared students at a liberal arts military academy. The previous version of the course was a traditional, lecture-based course that introduced circuits and software design. The new version of the course covers most of the same topics, but through a series of projects that culminate in a robotics maze competition. Redesign was motivated after two shortfalls were discovered: first, the number of electrical and computer engineering majors graduating each year was declining, and second, students graduating out of the major did not have necessary experience or knowledge in robotics.

Using best practices in engineering education, the course transitioned from a lecture model to a project-based learning model that includes three blocks over a forty-lesson semester: block 1, introductory topics; block 2, robotics design and implementation; and block 3, maze competition. Each laboratory includes a brief fifteen-minute introduction to a fundamental electrical and computer engineering concept and 3.5-hours of hands-on application. For example, after learning how the average power of a system can be controlled via pulse-width modulation, students integrate motors into the robot and connect each motor to a modern measurement tool to observe the digital pulse-width modulation signals sent to the robot and calculate the response time of the motors.

Evaluation measures include a pre/post survey that measure student excitement in the course, intent to major in electrical and computer engineering, and understanding of the field. Additionally, an exit survey upon graduation evaluates student intent to pursue a career in robotics. Lastly, registration data observes pre/post number of students in the major. Results show significant increases in interest in the field of electrical and computer engineering, number of majors, and student learning.

Introduction
Over the past ten years there has been a steady negative trend in the number of electrical and computer engineering (ECE) majors graduating from the United States Air Force Academy (USAFA). In 2010 there were 28 graduates. In 2020 there were 15 ECE graduates. This decline is not necessarily unique to USAFA. The United States saw only 10% of the global science, technology, engineering, and math (STEM) bachelor’s degrees in 2018 [1]. About half of students who enter a STEM program do not graduate with a STEM degree; most of these students drop out during their first or second year of college due to the increasing difficulty and complexity of STEM programs [2], [3], [4]. To motivate and engage students, undergraduate educators must design a curriculum that integrates hands-on learning early in the program that is relevant and can provide students a sense of ownership of their educations [5].

Additionally, engineers with robotics skills are specifically increasing in demand, but the needs are outpacing the workforce and a shortfall is emerging that undergraduate programs are not satisfying [6], [7], [8]. To fill both shortfalls, the number of ECE majors and those with a knowledge base in robotics, the Introduction to Electrical and Computer Engineering course was redesigned with two primary goals: first, increase recruitment for the ECE major and, second, spark interest in robotics. To accomplish these goals, the course was transitioned from a traditional, lecture-based course to a predominantly project-based course focused on the design and implementation of a robotics system shown in Figure 1, µSAFABOT.

This paper introduces µSAFABOT, a testbed developed to spark and promote undergraduate robotics research. The testbed is a modular platform built using additive technologies and an Arduino Uno that provides control of the on-board motors and sensors. This paper also describes how the introductory course was redesigned to teach students fundamental ECE skills through the implementation of µSAFABOT. The course also introduces complex robotics topics that are expanded on in a series of classes in a new robotics track in the major.


Figure 1: µSAFABOT.

Desired Objectives for Course
The objectives of the course were specifically aligned to the two goals of the course, increase recruitment for the ECE major and spark interest in robotics research. Robotics is a field that requires an understanding of topics covered throughout a typical ECE curriculum [9], therefore, this redesign focused on covering a broad spectrum of topics to provide a surface-level understanding of ECE and robotics skills that are expanded on in future courses. Most importantly, the course attempts to motivate students by focusing on hands-on experience and project-based learning, while also reaching the following educational objectives:

1. Prepare students for upper-level courses by teaching fundamental ECE tools and techniques.
2. Maximize student engagement.
3. Increase student understanding of the electrical and computer engineering field and major.
4. Increase student recruitment for the ECE major.
5. Facilitate student interest in robotics.

Theoretical Motivation
The theoretical motivation that drove course redesign was centered on evidence-based pedagogy pointing towards the benefits of project-based learning. Fundamentally, Kolb’s Experiential Learning Model asserts that a cycle of concrete experience, reflective observation, abstract conceptualization, and active experimentation results in higher student learning [10]. Implementation of Kolb’s method along with the integration of theory and hands-on practice in and introductory engineering course at Harvey Mudd College saw a statistically significant gain in student learning and an increased enthusiasm amongst female students [5]. To incorporate these theories, our course implemented cycling along with an increase in hands-on experience through the course structure. Students are introduced to fundamental ECE topics in block one through a series of hands-on laboratories. In block 2, students begin building their robots and must recall previous concrete experiences from block 1. They must reflect on how the topics they learned earlier in the class apply to the more complex example of a robot and experiment with these theories during robot development. Lastly, they must incorporate all previous lessons during block 3, maze competition.

The course redesign was also focused on developing professional traits that students could use in their careers as leaders in the United States Air Force. Findings show that active learning in the classroom provides longer-term benefits such as “career preparation, professional behaviors, and enhanced learning or learning processes” [11]. Team-based learning (TBL) also enhances professional skills and encourages collaboration, communication, and other interpersonal skills [12]. Part of the course redesign included an increase focus on engineering applications and collaboration. All labs allow students to work in small groups while building their individual robots.

Lastly, while there are no grades assigned in this course, frequent checkpoints allow for no-stakes testing which has been proven to increase student performance, especially in minorities [13]. Instead of taking tests, students work at their own pace to meet deliverable deadlines that they set individually. For example, a student may decide to have their motor driver and power distribution boards soldered by lesson 21. This form of contract learning enables students to work at their own pace to gain understanding [14] and empowers them to take responsibility for their education [15].

The µSAFABOT Testbed
Given the above motivation for hands-on project-based learning, we provide our µSAFABOT testbed. Built from the ground up by students, the testbed provides a platform for hands-on experimentation through ten laboratories.

Physical Platform
The platform for the µSAFABOT testbed includes the integration of three main components adapted from previous testbed designs [16]: a body, nerves, and brain.

The body of the testbed includes customizable 3D printed tiers that enable the mounting of motors, sensors, and other components. The µSAFABOT testbed’s current configuration can carry an Arduino Uno, Raspberry Pi 4, two direct current (DC) motors, three Sharp infrared distance sensors, and a Pololu QTR-8RC Reflectance Sensor Array. Mounting holes and slots in the layers provide flexibility to mount components in a variety of orientations. The testbed is powered using a pack of seven rechargeable AAA batteries stored on one of the layers.

The nerves consist of a custom printed circuit board (PCB) that provides voltage regulation and motor control. The PCB takes an input voltage between 7 V and 20 V and provides a fixed 3.3 V and 5 V output at a peak current of 250 mA and 1.5 A, respectively. An integrated motor driver chip converts direction and PWM signals from the Arduino Uno to power and control two DC motors.

The brain is an Arduino Uno Rev3. On-board sensors are connected to the brain using digital and analog input and output pins. The brain makes decisions and passes direction and speed (PWM) signals to the nerves using digital pins. The brain is powered using the 5 V/1.5 A output on the PCB.

Software Architecture
The software architecture is presented in Figure 2 and creates a control loop between the brain, nerves, and body. Starting at the brain, a controller process continuously polls the body for environment information from on-board sensors to inform the robot’s current state. The controller utilizes the current state information and sensor inputs to provide direction and PWM signals to the nerves. The nerves translate the control signal to drive the left and right motors accordingly, completing the loop.

Motivation
There are many off-the-shelf robotics kits available commercially [17], [18], [19]. However, from experience, many of these kits lose support over time, have difficult instructions, or have parts impossible to replace when a student inevitably breaks something. Building µSAFABOT from the ground up allows students to not only understand every interaction between each hardware and software component, but also allows instructors to easily replace parts or troubleshoot issues. The µSAFABOT system is less focused on fundamental understanding of each underlying system, but more on the integration, design, and motivation sides of student learning.

Future Work with the µSAFABOT Platform
One of the benefits of the µSAFABOT testbed is its modularity. Two areas currently under research to expand µSAFABOT’s capabilities are network connectivity and simulation. As previously mentioned, the body of the testbed can hold a Raspberry Pi 4. Two students are researching how to expand the power capabilities of the testbed to enable a Raspberry Pi 4 to act as a networked brain and allow a supervisor to wirelessly control the µSAFABOT. This would allow for the testing of more advanced artificial intelligence and teaming algorithms with the testbed. Additionally, students are working to model the µSAFABOT body and physical constraints to enable students to test their maze algorithms in simulation prior to implementing them on the real robot.


Figure 2: Architecture diagram for the µSAFABOT testbed.

µSAFABOT as an Introductory Educational Tool
The course redesign focused on effectively integrating the educational methods proposed by theory with the µSAFABOT testbed. Active learning techniques are designed into each lesson and, in keeping with TBL practices, students are encouraged to collaborate. As a result, students more advanced in a topic often assist those struggling around them, further forming their skills through helping their peers. The course consists of ten incremental laboratories which build on each other and culminate in a maze competition. At the beginning of each laboratory individual students agree to a deadline for completion promoting performance and removing anxiety regarding grades [14]. The course is broken into three blocks over a forty-lesson semester: block 1, introductory topics; block 2, robotics design and implementation; and block 3, maze competition.

Block 1: Introductory Topics
This course is the first engineering class for most students; therefore, four labs provide fundamental ECE skills and tools that are then used in building µSAFABOT in block 2. The course starts by introducing basic circuit troubleshooting techniques and tools. For example, students learn how to utilize a digital multimeter and other modern measurement tools to find circuit values. Unique to this course is Liquid Instrument’s Moku:Lab, a new device that integrates 12 tools into one system and enables cadets to learn how to use ECE tools with an iPad user interface as seen in Figure 3.


Figure 3: Liquid Instrument's Moku:Lab displaying PWM signal sent to one of the DC motors.

The next lab introduces additive manufacturing by training students to use LulzBot 3D printers and Fusion 360 modeling. Students pick an object to design and then print the model. These skills are called upon later to design and customize the µSAFABOT’s body in block 2. The students then learn how to solder with a basic soldering kit such as a burglar alarm or bagpipes. This prepares students to build the motor control and power distribution board for the robot. Lastly, the students learn how to program using an Arduino Uno and peripheral devices such as light-emitting diodes, switches, sonar sensors, and photoresistors. These skills are applied when programming the Arduino controller on the robot.

Block 2: Robotics Design and Implementation
The second block is designed to reflect a large-scale engineering project and uses an incremental approach observed in the spiral model or agile software development model. Each laboratory is presented as a distinct requirement and product solution. Students must stick to a deadline and work through an entire development process to plan, design, develop, test, and evaluate each component before moving to the next subsystem. Each lab corresponds to a specific engineering concept shown in Figure 4.


Figure 4: Correlation between engineering concept and corresponding µSAFABOT laboratory.

Students begin the robot build by developing the requirements for a motor controller and power distribution board. After students design their own solution, an operational circuit is provided to ensure success. The students must then solder the circuit, investigate specific test points, and troubleshoot if issues are found. The completed printed circuit board (PCB) is then integrated into a testbench that will demonstrate if all parts of the PCB are operational. Figure 5 provides a model of a completed printed circuit board without the off-the-shelf motor driver board (TB6612FNG Dual Motor Driver Carrier). The complete circuit diagram for the PCB is available in Appendix A.


Figure 5: 3D Model of the motor controller and power distribution board.

Next, students use additive manufacturing and modeling to design the robot body and build the robot. The body is fully customizable, but templates are provided as a starting point. Several off-the-shelf components (motors, nuts, bolts, switches, etc.) are integrated to the body to create the robot. The students must wire their PCB to the different systems before completing the robot per the robot circuit diagram provided in Figure 6. A picture of a student’s µSAFABOT mid-build is provided in Figure 7. Appendix B provides models for each of the 3D printed components of the robot, and Appendix C supplies the complete list of components used for the robot build.


Figure 6: Circuit diagram for the printed circuit board


Figure 7: Partially built µSAFABOT.

After building the robot, students test and characterize the motors using the Moku:Lab tool. They also program the motors to drive the robot in several different patterns. Students observe that there is no feedback from the motors, and, consequently, it is extremely difficult to drive the two motors at the same speed.

The last two labs include integrating the line following sensors and distance sensors. Both are calibrated and tested individually then integrated with the motors. The robot must follow a line, one wall, and stay between two walls. Basic control systems are introduced, and students design a proportional and integral controller to improve line and wall following.

Block 3: Maze Competition
The last block of the course integrates all previous labs as students compete in a maze competition. The maze competition demonstrates that interfacing embedded robotics systems with the physical world is a very complex task. The maze competition consists of three different levels, each presenting unique problems. The first level is a line following maze which challenges students to balance motor response with complex turns. Students must experimentally establish proportional constants to ensure their robot responds fast enough to follow the line through turns. The second level of the competition is wall following through a complex maze. Students experiment with different methods to turn and solve the maze in the quickest and most reliable manner (they must complete three successful time trials). The third level combines the two and requires students to transition between line following and wall following, seamlessly. A diagram of the maze is provided in Figure 8.


Figure 8: Maze with three levels (grey lines indicate walls, while black lines indicate line following tracks).

Evaluation Methods
The evaluation methods used to measure objectives are summarized in Table 1. Each method was used in the original course in Fall 2017 and repeated with the redesigned course in the Spring and Fall semesters of 2018, 2019, and 2020. A total of 70 students completed surveys over this period, 23 from the first course and 47 students from the revised course.

Table 1: Evaluation objectives and methods.

Evaluation Objectives | Method
Increase student preparedness for upper-level courses | Pre/post survey
Increase engagement | Pre/post survey and Student Evaluations of Teaching
Increase student understanding of the electrical and computer engineering field and major | Pre/post survey

Increase student recruitment for the ECE major
Facilitate student interest in robotics | Exit survey

The survey results include both quantitative and qualitative responses. Quantitative responses are based on a 5-point scale with 0 referring to a negative response and 5 referring to a positive test. The first student class to take the redesigned course graduated in May 2021; an exit survey was provided to these students requesting qualitative responses regarding the impact of the redesigned course in their interest to complete robotics research.

Results
The evaluation methods described above were used to assess the five desired course objectives. When applicable, a two-sample t-test with an alpha level of 0.05 was accomplished to demonstrate the significance of the redesign.
1. Increase student preparedness for upper-level courses.
Instructors were queried which key skills students should have experience with prior to upper-level courses. These skills included understanding of circuit analysis, soldering, electronic prototyping, software design, hardware troubleshooting, software troubleshooting, and use of MATLAB. The course is less focused on fundamental understanding of these key skills, and more on getting students familiarity with the topics. The topics are then expanded on in future course. Students were asked during pre-and post-course surveys what their experience level was for each of these skills and these responses were used to measure student preparedness for upper-level courses. The first column set in Figure 9 illustrates the improvement in student preparedness between courses. Students started both versions of the course with about the same level of knowledge, however, students in the new course felt more confident in their experience (3.57/5.0) compared to the old (3.15/5.0). Experience in ECE fundamentals increased significantly in the new course (1.92/5.0 to 3.57/5.0, p = 1.48 x 10⁻⁴⁸ < α).

Additionally, in an exit survey, seniors were asked, “Which topics in the introductory course were most helpful throughout your time in the ECE department?” One student responded, “The µSAFABOT was a fantastic introduction to all of the real applications of ECE that I built on in my other classes.” Another student enjoyed the incremental approach of the course and reported that the course was “perfectly designed and implemented such that each student had to understand each concept taught throughout the semester in order to be successful.”

2. Increase engagement.

Student engagement was measured during pre- and post-course surveys in which students were asked if they were excited about the course. The second column set in Figure 9 illustrates the increase in excitement between courses. Students began the course with an increased excitement compared to the previous version of the course (from 2.69/5.0 with the previous course to 3.26/5.0 for the new course; the increase is likely due to efforts to advertise the new version of the course and students hearing about the redesign and use of µSAFABOT from other students). The previous version of the course saw a slight increase in excitement levels (2.69/5.0 to 3.26/5.0, p = 0.02 < α), while the redesigned course saw a larger increase in excitement (3.17/5.0 to 4.11/5.0, p = 1.66 x 10⁻⁶ < α).

In the optional comments section of the survey for the new version of the course, one student reported, “This course has probably been my favorite course I have ever taken, not just at USAFA, but also in all my education thus far.” Another student who spent much more time than required working on µSAFABOT, said he did so “not because [he] had to, to earn a grade, but because [he] was engaged and passionate about the nature of the class and what [he] was learning.”

### 3. Increase student understanding of the electrical and computer engineering field and

major.
Student perception of their understanding of the ECE field and major was measured using the third survey item in Figure 9. Students in the new version of the course believed they had a better understanding of what it meant to be an ECE professional (4.27/5.0
compared to 3.20/5.0 in the old version).
4. Increase student recruitment for the ECE major.
Two forms of evaluation were used to determine if the new version of the course helped increase student recruitment: first, student intent to declare (fourth survey item results shown in Figure 9), and second, the number of students per class that declare. Both versions of the class saw an increase in the intent of students to declare (from 2.87/5.0 to 4.13/5.0 for the old version and from 3.09/5.0 to 4.36/5.0 for the new version). However, in the latest section of the revised course 79% of students in the course declare ECE, while the last section of the old version only saw 45% of students declare.

While it cannot be directly correlated to the course redesign, after the first year of the redesign the ECE department had the best recruiting class in 20 years with 65% diversity of candidates and 14 total females (more than the last 6 classes combined). The five student classes prior to the course redesign had an average of 22 ECE majors per class, while there has been an average of 31 ECE majors per year since the redesign.

5. Facilitate student interest in robotics.
Student interest in robotics was one of the more difficult goals to measure. Prior to the course redesign there was no focus on robotics in the course. The course’s impact on robotics through the µSAFABOT testbed was primarily measured using student comments in the post-survey. One student commented that the course “motivated [him] to pursue graduate school for robotics and become an instructor at USAFA through the graduate school program.” Another student saw the hands-on format of the class and focus on µSAFABOT “lead [him] to take more in-depth robotics courses…and an internship with the NSA focusing on Artificial Intelligence and Machine Learning.”

During the second iteration of the new course, instructors were advised to identify students with an advanced ability in robotics. A total of eight students were identified and targeted for robotics research in the department. Two years later, these eight cadets have accomplished over 24 semester hours of robotics research, developed an Introduction to Robotics Research course, and competed in robotics competitions. These students might not have been identified if the course was not centered around the hands-on, project-based model.

Knowledge of fundamentals; Excitement of course; Understanding what an; ECE major does; To what extent are you considering ECE as a major (only undeclared); Average student response; (based on a 5-point scale); Pre survey results, original course; Post survey results, original course; Pre survey results, new course; Post survey results, new course

Figure 9: Pre/post survey results for original and new course (N=23 for the original course; N=47 for revised course).

Conclusion
Three years ago, USAFA’s Introduction to Electrical and Computer Engineering course was redesigned. Driven by a ten-year negative trend in the number of students declaring as ECE majors and a lack of robotics knowledge, the course was transitioned from a lecture-based class to primarily hands-on and project-based. Motivated by similar successes at Harvey Mudd College and Kolb’s Experiential Learning Theory, the course was designed to revolve around a robotics system designed by USAFA instructors, µSAFABOT. The µSAFABOT testbed is a modular robotics system that enables students to experiment with ECE fundamentals while building a robot from the ground up. Based on an incremental approach, lessons builds on each other and culminate in a maze competition. Students learn about the spiral dsign process as each lab requires them to stick to a schedule as they plan, design, develop, test, and evaluate each subsystem before moving to the next subsystem.

Results of pre/post surveys, a senior exit survey, registrar data, and student feedback show that there was a significant increase in student excitement and understanding regarding the field of ECE. Additionally, the course accomplished its goal of increasing recruitment in the major as the number of majors per year on average increased by 41%. Lastly, the course transition sparked an interest in robotics throughout the department and students. Overall, this course redesign has been very successful, and the department head even fights to teach it.

For more information on the technical implementation details and to implement the laboratories associated with µSAFABOT, please refer to https://github.com/AF-ROBOTICS/DFEC_RoboticsLearningPlatform.

References

[1] National Science Board, “Science & Engineering Indicators 2018,” National Science Foundation, Alexandria, VA, USA, NSB-2018-1, 2018. Accessed: Mar 4, 2021. [Online]. Available: https://www.nsf.gov/statistics/indicators/.
[2] X. Chen, “STEM Attrition: College Students' Paths Into and Out of STEM Fields,” National Center for Education Statistics, Institute of Education Sciences, U.S. Department of Education, Washington, DC, USA, NCES-2014-001, 2013. Accessed: Sep 15, 2020. [Online]. Available: https://nces.ed.gov/pubs2014/2014001rev.pdf.
[3] E. Seymour and N. M. Hewitt, Talking about leaving: Why undergraduates leave the sciences. Boulder, CO, USA: Westview Press, 2000.
[4] C. Drew. “Why Science Majors Change Their Minds (It's Just So Darn Hard).” The New York Times, November 4, 2011. Accessed: Mar 1, 2021. [Online]. Available: https://www.nytimes.com/2011/11/06/education/edlife/why-science-majors-change-their-mind-its-just-so-darn-hard.html. (https://www.nytimes.com/2011/11/06/education/edlife/why-science-majors-change-their-mind-its-just-so-darn-hard.html)
[5] Lape, Nancy K., et al. "Integrating Theory and Hands-On Practice using Underwater Robotics in a Multidisciplinary Introductory Engineering Course." 2017 ASEE Annual Conference & Exposition. ASEE Conferences, Columbus, Ohio. https://peer.asee.org/28561. 2017. (https://peer.asee.org/28561.%202017)
[6] U.S. Bureau of Labor Statistics, “Occupational Outlook Handbook: Mechanical Engineers,” 2017. Accessed: Mar 1, 2021. [Online]. Available: https://www.bls.gov/ooh/architecture-and-engineering/mechanical-engineers.htm/. (https://www.bls.gov/ooh/architecture-and-engineering/mechanical-engineers.htm/)
[7] R. Thomas, R. Bhat, A. Khan, and P. Devan, “2018 Deloitte and the Manufacturing Institute skills gap and future of work study,” Delloitte Development LLC, 2018. Accessed: Mar 1, 2021. [Online]. Available: https://www.themanufacturinginstitute.org/wp-content/uploads/2020/03/MI-Deloitte-skills-gap-Future-of-Workforce-study-2018.pdf. (https://www.themanufacturinginstitute.org/wp-content/uploads/2020/03/MI-Deloitte-skills-gap-Future-of-Workforce-study-2018.pdf)

[8] E. Demaitre. “Robots.Jobs addresses robotic skills shortage with a national approach.” The Robot Report, February 6, 2019. Accessed: Mar1, 2021. [Online] Available: https://www.therobotreport.com/robots-jobs-addresses-skills-shortage/.
[9] H. C. Powell and J. B. Dugan, “Embedded and cyber-physical computing courseware as the nexus of curriculum reform in electrical and computer engineering,” in Proc of ASEE-SE Section, Macon, GA, USA: ASEE, 2014.
[10] Kolb, David A. "Management and the learning process." California management review 18.3 (1976): 21-31.
[11] Clark, Renee M., Autar Kaw, and Mary Besterfield-Sacre. "Comparing the effectiveness of blended, semi-flipped, and flipped formats in an engineering numerical methods course." Advances in Engineering Education 5.3 (2016): n3.
[12] Michaelsen, Larry K., Arletta Bauman Knight, and L. Dee Fink, eds. Team-based learning: A transformative use of small groups. Greenwood publishing group, 2002.
[13] Haak, David C., et al. “Increased structure and active learning reduce the achievement gap in introductory biology.” Science 332, no. 6034 (2011): 1213-1216.
[14] H. Taylor, “Contract grading,” Nat. Inst. Educ., 1980.
[15] C. A. Tomlinson, The Differentiated Classroom: Responding to the Needs of All Learners. Upper Saddle River, NJ: Merrill-Prentice-Hall, 1999.
[16] T. L. Crenshaw and S. Beyer, “UPBOT: A testbed for cyber-physical systems,” in Proc of the 3rd CSET, Aug. 2010, Article no. 1-8.
[17] “Arduino Robot,” Arduino Store. Accessed: Mar 4, 2021. [Online]. Available: https://store.arduino.cc/usa/arduino-robot.
[18] “Pololu 3pi Robot,” Pololu Robotics & Electronics. Accessed: Mar 4, 2021. [Online]. Available: https://www.pololu.com/category/279/original-3pi-robot.
[19] “SparkFun micro:bot kit for micro:bit - v2.0,” sparkfun. Accessed: Mar 4, 2021. [Online]. Available: https://www.sparkfun.com/products/16275.

Appendix A. Motor Controller and Power Distribution Board Circuitry.


Appendix B. 3-Dimensional Models of µSAFABOT Testbed.


Appendix C. On-Board Sensors.



Appendix D. Example Laboratory








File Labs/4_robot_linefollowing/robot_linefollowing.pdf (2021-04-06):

ECE210: Introduction to Electrical and Computer Engineering

# Robot Line Following


1 Objectives.

1. Become familiar with the QTR-8RC Line Sensor Array.
2. Utilize the Arduino to detect lines.
3. Integrate the Line Sensors with the DFECBot and program the DFECBot to follow a line.

2 Materials.

1. 1x QTR-8RC Reflectance Sensor Array
2. DFECBot
3. USB Programming Cable
4. Black Tape

3 Introduction.

### 3.1 QTR-8RC Reflectance Sensor Array

The QTR-8RC Line Sensor Array uses 8 infrared radiation (IR) reflectance sensor with an IR light-emitting diode (LED) and an IR sensitive phototransistor.¹ The sensors are powered using the 3.3 V and ground pins on the Arduino. Powering the sensors illuminates the IR LED. A 100 Ω resistor is on-board and placed in series with the LED to limit current. The output of the phototransistor is tied to a 10 nF capacitor. The

1
Information found at Pololu, https://www.pololu.com/product/961

ECE210: Introduction to Electrical and Computer Engineering -Robot Line Following

faster the capacitor discharges, the more reflective the surface is.¹ The QTR sensors have an optimal sensing distance of 3 mm.

Wire your QTR-8RC Reflectance Sensor Array to the Arduino according to the schematic shown in Figure 1.


Figure 1: QTR-8RC Reflectance Sensor Array Wiring Schematic

### 3.2 Example Code

Copy the Arduino sketch folder robot_linefollowing from Teams (Labs/robot_linefollowing).
Copy the QTR-8RC library from Teams (Labs/Custom Libraries/QTR-8RC) to your documents folder:
Documents/Arduino/libraries/. Open the robot_wallfollowing.ino sketch.

### 3.3 QTR-8RC.h

The Arduino Sketch utilizes a library called QTR-8RC. This is a custom library adapted from the QTRSensors library to utilize the QTR-8RC Reflectance Sensor Array. This library provides functions to read values from the sensor array and return the distance off the line.

### 3.3.1 robot linefollowing.ino

This example Arduino Sketch provides code to calibrate the DFECBot’s QTR-8RC Reflectance Sensor Array and determine the distance off a black line.

1 | // re ad c a l i b r a t e d s e n s o r v al u e s and o b t ai n a measure o f the l i n e p o s i t i o n
2 | // with a p o s i t i o n o f 0. 1 mm r e l a t i v e t o the c e n t e r o f the l i n e
3 | // −33.2 mm t o 3 3. 2 mm
4 | i n t 1 6 t p o s i t i o n = q t r . re a dLi neBl a c k ( s e n s o rV al u e s ) ;

### 4 Procedure

Use the example code provided, robot_linefollowing, Motor.h, and QTR-8RC.h to code the DFECBot to do the following:

1. Use a ruler to confirm the accuracy of the line sensor read function
2. Program the DFECBot to follow a line

ECE210: Introduction to Electrical and Computer Engineering -Robot Line Following

CALIBRATION: The first 10 seconds after powering on your robot (or uploading the code) is used to calibrate your line sensor. During calibration, without lifting your robot off the surface, slowly move your robot so each line sensor is over a black line for approximately one second. This allows the script to collect minimum (white surface) and maximum (black surface) readings used to calibrate the sensors.

HINT: You should remove all print statements and delays when testing your line following.

### 5 Notes on Proportional Controller:

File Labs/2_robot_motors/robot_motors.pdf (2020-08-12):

ECE210: Introduction to Electrical and Computer Engineering

# Robot Motors


1 Objectives.

1. Understand the fundamentals of Pulse Width Modulation (PWM) including period, frequency, duty cycle, and pulse width.
2. Understand how PWM can be used to control the speed of motors.
3. Demonstrate understanding by manipulating the motors at different speeds.

2 Pre-lab - To be done prior of class.

### 2.1 Reading:

Adapted from Embedded Systems: Real-Time Interfacing to the MSP432 Microcontroller, Jonathan W. Valvano, Third Edition, 2019.

One effective way to deliver power to a DC motor in a variable manner is to use pulse width modulation (PWM). The basic idea of PWM is to create a digital output wave of fixed frequency, but allow the microctonroller to vary its duty cycle. The system is designed in such a way that High+Low is constant (meaning frequency/period is fixed). The duty cycle is defined as the fraction of time the signal is high:

duty cycle =

High
High + Low

=

High
P eriod

Hence, duty cycle varies from 0 to 1 and will often be referred to as a percent. We interface this digital output wave to an external actuator (like a DC motor), such that power is applied to the motor when the signal is high, and no power is applied when the signal is low. We purposely select a frequency high enough so the DC motor does not start/stop with each individual pulse, but rather responds to the overall average value of the wave.

ECE210: Introduction to Electrical and Computer Engineering -Robot Motors

### 2.2 Key Terms:

| Pulse Width Modulation (PWM): A technique to deliver a variable signal (power) using an on/off signal with a variable percentage of time the signal is on (duty cycle).
| Period/Frequency: Time required to complete one full cycle (on/off). Frequency is the inverse of period and is constant. The Arduino pins used by the robot operate at 980 Hz.
| Duty Cycle: Percentage of time a digital signal is on over a period of time

### 2.3 Examples:


1. Pulsing an LED on and off.


You have already applied PWM to pulse the red LED using the Arduino. You varied the duty cycle through the use of the analogWrite() function within the for-loop which varied the power applied to the LED and consequently, the brightness. The code you used is to the right.

2. Answer the following given the example shown below in Figure 1.
(a) What is the period of the signal?
(b) What is the pulse width of the signal (how long is the signal HIGH)?
(c) What is the duty cycle?


Figure 1

3. Given that the analogWrite(pin, value) function’s value parameter is an integer that represents the duty cycle between 0 (always off) and 255 (always on), what would be the value passed to provide a 75% duty cycle to the motors?

### 2.4 Code:

1. Copy the Arduino sketch folder robot_motors from Teams (Labs/robot_motor)
2. Open the robot_motors.ino sketch.
3. In the loop() function, update the five calls to Motor Forward() to drive the motor at the designated duty cycles.

The example provided, Motor Forward(50, 50);, will drive both the left and right motors at (50/255)% of the duty cycle. This is equivalent to a duty cycle of about 20%.

4. Upload the sketch to the robot. Both motors of the robot should now operate at 6 different speeds (from 20% duty cycle up to 100% and back down to 15%).

3 Lab.

This lab will demonstrate how varying the PWM signal changes the average power delivered to the DC motors and, effectively, the speed of the motors.

### 3.1 Materials:

1. Assembled BeyerBot
2. Arduino programming cable
3. Laptop
4. Male-to-female/male Y-connector and male-to-male wire (provided for you in the Moku:Lab)

### 3.2 Connect the Moku:Lab probes:

1. Disconnect ONLY the wire from Pin-5 on the Arduino.
2. Insert male end of the Y-connector into Pin-5.
3. Connect the male end of the wire coming from your Printed Circuit Board (the one disconnected from Pin-5 ) into the female end of the Y-connector.
4. Connect the positive (red) end of the Moku:Lab probe to Pin-5 on the Arduino using the Y-connector.
5. Insert a male-to-male wire into the GND-Pin on the Arduino and connect the ground (black) end of the Moku:Lab probe to the other end of the wire.
6. Your setup should now look like Figure 2. All other wires should still be connected as they were previously.


Figure 2


### 3.3 Measuring Pulse Width Modulation Signals:

1. Place your robot on the Digital Multi Meter (DMM) (to allow the program to run without your robot driving away)
2. Your Moku:Lab display should look like Figure 3. If it does not, raise your hand.

Figure 3

3. Open the measurements bar by pressing the ruler in the bottom right of your screen.


4. Add three measurement tools: Frequency, Period, and Pulse width. Press the “plus” sign within the measurements toolbox to add a new tool. Select the tool to change it. Repeat this for each of the four tools.


5. Turn on your robot and run the previously uploaded code.
6. What do you notice?
7. Comment out all of the code within loop() except for the portion that runs the motors at 75% duty cycle (Motor Forward(191,191); delay(2000);) and answer the following questions:
(a) What is the frequency of the signal?
(b) What is the period of the signal?
(c) What is the pulse width of the signal (how long is the signal HIGH)?
(d) Using these values, calculate the duty cycle.
(e) Is this duty cycle what you expected?
(f) Add a Duty cycle measurement tool on the display (reference step 4.3-4). Does the value match what you calculated?
(g) How does the speed of the motors correlate to the duty cycle?

4 Feedback.

1. Was there any part of the lab that was confusing or unclear?
2. Is there any aspect of PWM that you still find confusing or would like more clarification on?
3. What would you change from this lab for next semester?

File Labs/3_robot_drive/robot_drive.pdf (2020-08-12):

ECE210: Introduction to Electrical and Computer Engineering

# Drive Robot


1 Objectives.

1. Become familiar with the DFECBot driving functions.
2. Utilize the Arduino to drive the robot in multiple patterns.

2 Materials.

1. DFECBot
2. USB Programming Cable

3 Introduction.

### 3.1 Source Files

Download the robot_drive folder from Teams (Labs/drive_robot). Open robot_drive.ino.

Use Notepad++ to open the Motor.h file that you previously saved here: Documents/Arduino/libraries/Motor/Motor.h. The .h file is a header file used within the .ino Arduino sketch. Take a look at Motor.h first.

ECE210: Introduction to Electrical and Computer Engineering -Drive Robot

### 3.1.1 Motor.h

This file uses four pins on the Arduino to communicate with the TB6612FNG Motor Driver chip on your PCB board. These pins are used as follows:

Pin 2 (L DIR)– Connects to the APS CTRL pin on the PCB board. This pin sends a signal to the motor driver to control the direction of the left motor.

Pin 3 (L PWM) – Connects to the APS MA pin on the PCB board. This pin sends a Pulse Width Modulation (PWM) signal to the motor driver to control the speed of left motor.

Pin 4 (R DIR)– Connects to the BPS CTRL pin on the PCB board. This pin sends a signal to the motor driver to control the direction of the right motor.

Pin 5 (R PWM)– Connects to the BPS MB pin on the PCB board. This pin sends a Pulse Width Modulation (PWM) signal to the motor driver to control the speed of right motor.

In the Motor Init function, all four of these pins are set to OUTPUT pins.

The Motor.h file provides basic drive functions like Motor Forward(leftDuty, rightDuty) and Motor Stop(). All movement functions (Motor Forward, Motor Left, etc) will run until the next movement function is provided. For example, to get the robot to move forward for 5 seconds then stop, the Motor Forward(leftDuty, rightDuty) function should be called followed by a 5 second delay and the Moto Stop() function.

### 3.1.2 robot drive.ino

This is the main file to place drive code. This file is reliant on the Motor.h header file. The robot\ _drive.ino file provides an example to move the robot forward, turn left, turn right, drive backwards, and then stop. This code will repeat continuously until the DFECBot is powered off (See below code). Delete this example code before submission.

1 | /*
2 | * | Code t o make the DFECBot go forward , tu rn l e f t , tu rn ri g h t , go
3 | * | backward and s t o p . This code w i l l r e p e a t c o n ti n u o u sl y
4 | * | u n t i l the DFECBot i s powered o f f
5 | */
6 | Motor Forward ( l e f tD u t y , ri gh tDu ty ) ;
7 | d el a y ( 2 0 0 0 ) ;
8 | M o t o r Le f t ( l e f tD u t y , ri gh tDu t y ) ;
9 | d el a y ( 2 0 0 0 ) ;
10 | Motor Right ( l e f tD u t y , ri gh tDu t y ) ;
11 | d el a y ( 2 0 0 0 ) ;
12 | Motor Backward ( l e f tD u t y , ri gh tDu t y ) ;
13 | d el a y ( 2 0 0 0 ) ;
14 | Motor Stop ( ) ;
15 | d el a y ( 2 0 0 0 ) ;

### 4 Procedure

Use the example code provided and the Motor.h to code the DFECBot to drive the following patterns. The DFECBot should pause for 2 seconds between each pattern.

1. Drive the DFECBot forward.
(a) Drive forward for 5 seconds.
2. Drive the DFECBot forward and reverse.
(a) Drive forward for 5 seconds.
(b) Pause for 1 second.
(c) Drive in reverse for 5 seconds to return to the starting position.

ECE210: Introduction to Electrical and Computer Engineering -Drive Robot

3. Drive the DFECBot forward, turn around, and return to start.
(a) Drive forward for 5 seconds.
(b) Pause for 1 second.
(c) Turn around.
(d) Drive back to start and original orientation.
4. Drive the DFECBot in a square.
(a) Drive in a square making right turns.
(b) Return to the starting location and position.
(c) Drive in a square making left turns.
(d) Return to the starting location and position.
5. Drive the DFECBot in a small circle.
(a) Drive in a clockwise circle keeping one wheel fixed.
(b) Drive in a counter clockwise circle keeping one wheel fixed.
6. Drive the DFECBot in a large circle.
(a) Drive in a clockwise circle with an approximate diameter of 2 feet.
(b) Drive in a counter clockwise circle with an approximate diameter of 2 feet.
7. Drive the DFECBot in a pattern of choice.
(a) Drive in a pattern of your choosing.

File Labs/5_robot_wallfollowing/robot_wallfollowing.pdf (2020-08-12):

ECE210: Introduction to Electrical and Computer Engineering | Spring 2019

# Robot Wall Following


1 Objectives.

1. Become familiar with the Sharp GP2Y0A51SK0F Analog Distance Sensor.
2. Utilize the Arduino to detect walls.
3. Integrate the Distance Sensor with the DFECBot and program the DFECBot to avoid obstacles.

2 Materials.

1. 3x Sharp GP2Y0A51SK0F Analog Distance Sensor
2. USB Programming Cable
3. DFECBot

ECE210: Introduction to Electrical and Computer Engineering - Spring 2019 Robot Wall Following

3 Introduction.

### 3.1 Sharp GP2Y0A51SK0F Analog Distance Sensor

The Sharp GP2Y0A51SK0F Analog Distance Sensor uses an infrared radiation (IR) reflectance sensor with an IR light-emitting diode (LED) and an IR sensitive phototransistor.¹Ensure your three sensors are wired per the below diagram.


Figure 1: Sharp GP2Y0A51SK0F Analog Distance Sensor Wiring Schematic

### 3.2 Example Code

Copy the Arduino sketch folder robot_wallfollowing from Teams (Labs/robot_wallfollowing). Open the robot_wallfollowing.ino sketch.

### 3.2.1 SharpDistanceSensor.h

The Arduino Sketch utilizes a library called SharpDistSensor. This library provides functions to read values from the Sharp IR sensors. You need to install this library for the example code to work.

1. Click Tools → Manage Libraries
2. Search for SharpDistSensor
3. Select Install

### 3.2.2 robot wallfollowing.ino

This example Arduino Sketch provides code to read the values from the DFECBot’s right Distance Sensor (see below example) and provides a distance value in mm.

1 | // Read di s t a n c e ( i n mm) f o r each s e n s o r
2 | un si gned i n t di s tR = senso rR . g e t Di s t ( ) + OFFSET;
3 | S e r ia l . p ri n t ( ”Right : ” ) ; S e r ia l . p r i n t l n ( di s tR ) ;

1GP2Y0A51SK0F Datasheet, https://www.pololu.com/file/0J845/GP2Y0A41SK0F.pdf.pdf

ECE210: Introduction to Electrical and Computer Engineering - Spring 2019 Robot Wall Following

### 4 Procedure

Use the example code provided to code the DFECBot to do the following:

1. Print the values from the DFECBot’s center and left GP2Y0A51SK0F Analog Distance Sensor to the serial monitor.
2. Use a ruler to confirm the accuracy of each distance sensor - the sensor should be fairly accurate between 3 cm and 12 cm.
3. Program the DFECBot to follow wall on right.
4. Program the DFECBot to follow wall on left.
5. Program the DFECBot to stay between two walls.

HINT: You should remove all print statements and delays when testing your wall following.

### 5 Notes on Proportional Controller:

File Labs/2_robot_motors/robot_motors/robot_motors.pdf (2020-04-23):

ECE210: Introduction to Electrical and Computer Engineering

# Robot Motors

1 Objectives.

1. Understand the fundamentals of Pulse Width Modulation (PWM) including period, frequency, duty cycle, and pulse width.
2. Understand how PWM can be used to control the speed of motors.
3. Demonstrate understanding by manipulating the motors at different speeds.

2 Pre-lab - To be done prior of class.

### 2.1 Reading:

Adapted from Embedded Systems: Real-Time Interfacing to the MSP432 Microcontroller, Jonathan W. Valvano, Third Edition, 2019.

One effective way to deliver power to a DC motor in a variable manner is to use pulse width modulation (PWM). The basic idea of PWM is to create a digital output wave of fixed frequency, but allow the microctonroller to vary its duty cycle. The system is designed in such a way that High+Low is constant (meaning frequency/period is fixed). The duty cycle is defined as the fraction of time the signal is high:

duty cycle =

High
High + Low

=

High
P eriod

Hence, duty cycle varies from 0 to 1 and will often be referred to as a percent. We interface this digital output wave to an external actuator (like a DC motor), such that power is applied to the motor when the signal is high, and no power is applied when the signal is low. We purposely select a frequency high enough so the DC motor does not start/stop with each individual pulse, but rather responds to the overall average value of the wave.

### 2.2 Key Terms:

| Pulse Width Modulation (PWM): A technique to deliver a variable signal (power) using an on/off signal with a variable percentage of time the signal is on (duty cycle).
| Period/Frequency: Time required to complete one full cycle (on/off). Frequency is the inverse of period and is constant. The Arduino pins used by the robot operate at 980 Hz.
| Duty Cycle: Percentage of time a digital signal is on over a period of time


ECE210: Introduction to Electrical and Computer Engineering -Robot Motors

### 2.3 Examples:

1. Pulsing an LED on and off.

You have already applied PWM to pulse the red LED using the Arduino. You varied the duty cycle through the use of the analogWrite() function within the for-loop which varied the power applied to the LED and consequently, the brightness. The code you used is to the right.


2. Answer the following given the example shown below in Figure 1.
(a) What is the period of the signal?
(b) What is the pulse width of the signal (how long is the signal HIGH)?
(c) What is the duty cycle?


Figure 1

3. Given that the analogWrite(pin, value) function’s value parameter is an integer that represents the duty cycle between 0 (always off) and 255 (always on), what would be the value passed to provide a 75% duty cycle to the motors?

### 2.4 Code:

1. Copy the Arduino sketch folder robot_motors from Teams (Labs/robot_motor)
2. Open the robot_motors.ino sketch.
3. In the loop() function, update the five calls to Motor Forward() to drive the motor at the designated duty cycles.

The example provided, Motor Forward(50, 50);, will drive both the left and right motors at (50/255)% of the duty cycle. This is equivalent to a duty cycle of about 20%.

4. Upload the sketch to the robot. Both motors of the robot should now operate at 6 different speeds (from 20% duty cycle up to 100% and back down to 15%).

3 Lab.

This lab will demonstrate how varying the PWM signal changes the average power delivered to the DC motors and, effectively, the speed of the motors.

### 3.1 Materials:

1. Assembled BeyerBot
2. Arduino programming cable
3. Laptop
4. Male-to-female/male Y-connector and male-to-male wire (provided for you in the Moku:Lab)

### 3.2 Connect the Moku:Lab probes:

1. Disconnect ONLY the wire from Pin-5 on the Arduino.
2. Insert male end of the Y-connector into Pin-5.
3. Connect the male end of the wire coming from your Printed Circuit Board (the one disconnected from Pin-5 ) into the female end of the Y-connector.
4. Connect the positive (red) end of the Moku:Lab probe to Pin-5 on the Arduino using the Y-connector.
5. Insert a male-to-male wire into the GND-Pin on the Arduino and connect the ground (black) end of the Moku:Lab probe to the other end of the wire.
6. Your setup should now look like Figure 2. All other wires should still be connected as they were previously.


Figure 2

### 3.3 Measuring Pulse Width Modulation Signals:

1. Place your robot on the Digital Multi Meter (DMM) (to allow the program to run without your robot driving away)
2. Your Moku:Lab display should look like Figure 3. If it does not, raise your hand.

Figure 3


3. Open the measurements bar by pressing the ruler in the bottom right of your screen.
4. Add three measurement tools: Frequency, Period, and Pulse width. Press the “plus” sign within the measurements toolbox to add a new tool. Select the tool to change it. Repeat this for each of the four tools.


5. Turn on your robot and run the previously uploaded code.
6. What do you notice?

7. Comment out all of the code within loop() except for the portion that runs the motors at 75% duty cycle (Motor Forward(191,191); delay(2000);) and answer the following questions:
(a) What is the frequency of the signal?
(b) What is the period of the signal?
(c) What is the pulse width of the signal (how long is the signal HIGH)?
(d) Using these values, calculate the duty cycle.
(e) Is this duty cycle what you expected?
(f) Add a Duty cycle measurement tool on the display (reference step 4.3-4). Does the value match what you calculated?
(g) How does the speed of the motors correlate to the duty cycle?

4 Feedback.

1. Was there any part of the lab that was confusing or unclear?
2. Is there any aspect of PWM that you still find confusing or would like more clarification on?
3. What would you change from this lab for next semester?

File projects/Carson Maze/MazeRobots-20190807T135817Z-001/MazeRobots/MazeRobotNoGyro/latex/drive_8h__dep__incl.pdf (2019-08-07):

PCB_test/PCB_test/drive.h

PCB_test/PCB_test/PCB
_test.ino

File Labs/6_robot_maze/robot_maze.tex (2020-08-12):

\documentclass{handout}

%\SetInstructor{Capt Steven Beyer}
\SetCourseTitle{ECE210: Introduction to Electrical and Computer Engineering}
\SetHandoutTitle{Robot Maze}

%\ShowAllBlanks

\usepackage[obeyspaces]{url}

\graphicspath{{./figs/}}

%\showsoln \setsolncolor{red}

\begin{document}
	%	\footnotetext{Examples are abstracted from Tutorials Point, "Arduino", 2019, accessed Feb 18, 2019. [Online]. Available: https://www.tutorialspoint.com/arduino/index.htm}
	\maketitle
	\begin{figure}[H]
		\centering
		
	\end{figure}
	
	\section{Objectives.} 
	\begin{enumerate}
		\item Combine previous labs into a system that solves a complex task. 
		\item Troubleshoot ECE applications.
		\item Combine multiple systems (e.g., line following and wall detection) to build a more complex system.
	\end{enumerate}
	
	\section{Materials.}
	\begin{enumerate}
		\item DFEC Robot
		\item Maze
	\end{enumerate}
	
	\section{Robot Maze - Level 1: Line Following}
	The first level of the maze requires the robot to follow a white line to the end of the maze.
	
	\section{Robot Maze - Level 2: Advanced Line Following}
	The second level of the maze requires the robot to follow a white line to the end of the maze, detect the wall, turn around, and follow the line to the beginning of the maze, detect the wall, turn around, and stop.
	
	\section{Robot Maze - Level 3: Navigate Maze}
	The third level of the maze requires the robot to navigate the maze until it reaches the goal in the middle of the maze. It does not need to do anything special once it reaches the goal. Reaching the goal is enough.
	
	\section{Competition}
	The best times for each level will be recorded and displayed on a plaque in the ECE210 room.
\end{document}

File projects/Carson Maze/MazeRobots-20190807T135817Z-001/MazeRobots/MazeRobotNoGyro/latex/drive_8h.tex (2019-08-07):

\hypertarget{drive_8h}{}\section{P\+C\+B\+\_\+test/\+P\+C\+B\+\_\+test/drive.h File Reference}
\label{drive_8h}\index{P\+C\+B\+\_\+test/\+P\+C\+B\+\_\+test/drive.\+h@{P\+C\+B\+\_\+test/\+P\+C\+B\+\_\+test/drive.\+h}}

Contains mid-\/level drive commands for the robot, such as driving forward and turning.  

{\ttfamily \#include \char`\"{}T\+B6612\+F\+N\+G.\+h\char`\"{}}\newline
{\ttfamily \#include $<$Encoder.\+h$>$}\newline
{\ttfamily \#include \char`\"{}util.\+h\char`\"{}}\newline
Include dependency graph for drive.\+h\+:
\nopagebreak
\begin{figure}[H]
\begin{center}
\leavevmode

\end{center}
\end{figure}
This graph shows which files directly or indirectly include this file\+:
\nopagebreak
\begin{figure}[H]
\begin{center}
\leavevmode

\end{center}
\end{figure}
\subsection*{Classes}
\begin{DoxyCompactItemize}
\item 
class \hyperlink{classRobot}{Robot}
\end{DoxyCompactItemize}
\subsection*{Functions}
\begin{DoxyCompactItemize}
\item 
\mbox{\Hypertarget{drive_8h_a83d1a5e8551e4f9461bc5beb6026fdd8}\label{drive_8h_a83d1a5e8551e4f9461bc5beb6026fdd8}} 
double {\bfseries degrees\+To\+Edges} (double deg)
\end{DoxyCompactItemize}
\subsection*{Variables}
\begin{DoxyCompactItemize}
\item 
\mbox{\Hypertarget{drive_8h_a9b48e465bd56bdf84200e8ca183976db}\label{drive_8h_a9b48e465bd56bdf84200e8ca183976db}} 
constexpr const double {\bfseries edges\+\_\+per\+\_\+mm} = 9.\+4024 $\ast$ 0.\+813
\end{DoxyCompactItemize}

\subsection{Detailed Description}
Contains mid-\/level drive commands for the robot, such as driving forward and turning.

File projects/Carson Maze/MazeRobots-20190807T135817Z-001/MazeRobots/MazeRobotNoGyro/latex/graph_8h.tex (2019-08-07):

\hypertarget{graph_8h}{}\section{P\+C\+B\+\_\+test/\+P\+C\+B\+\_\+test/graph.h File Reference}
\label{graph_8h}\index{P\+C\+B\+\_\+test/\+P\+C\+B\+\_\+test/graph.\+h@{P\+C\+B\+\_\+test/\+P\+C\+B\+\_\+test/graph.\+h}}

Contains the structure of the maze and functions to alter the robot\textquotesingle{}s relation to the grid.  

{\ttfamily \#include \char`\"{}util.\+h\char`\"{}}\newline
Include dependency graph for graph.\+h\+:
\nopagebreak
\begin{figure}[H]
\begin{center}
\leavevmode

\end{center}
\end{figure}
This graph shows which files directly or indirectly include this file\+:
\nopagebreak
\begin{figure}[H]
\begin{center}
\leavevmode

\end{center}
\end{figure}
\subsection*{Classes}
\begin{DoxyCompactItemize}
\item 
struct \hyperlink{structCell}{Cell}
\end{DoxyCompactItemize}
\subsection*{Functions}
\begin{DoxyCompactItemize}
\item 
\mbox{\Hypertarget{graph_8h_a70bc642a7c7b9b1a4752cf04d689e5ec}\label{graph_8h_a70bc642a7c7b9b1a4752cf04d689e5ec}} 
void {\bfseries move\+In} (\hyperlink{util_8h_a92e22a126ad6bf9d255b517e70d083f6}{Direction} dir)
\item 
\hyperlink{util_8h_a92e22a126ad6bf9d255b517e70d083f6}{Direction} \hyperlink{graph_8h_ab4afdc4009e71e9811133449a48262c6}{get\+Relative\+Heading} (int offset)
\end{DoxyCompactItemize}
\subsection*{Variables}
\begin{DoxyCompactItemize}
\item 
\mbox{\Hypertarget{graph_8h_af1b7aa56fe5bbc2c1965c92ea3c6b1a4}\label{graph_8h_af1b7aa56fe5bbc2c1965c92ea3c6b1a4}} 
constexpr const float {\bfseries wall\+\_\+thickness} = 12.\+0
\item 
\mbox{\Hypertarget{graph_8h_ae09ec5e6a6fc4579aec5c96e98ab72da}\label{graph_8h_ae09ec5e6a6fc4579aec5c96e98ab72da}} 
constexpr const float {\bfseries cell\+\_\+width} = 167.\+0 + wall\+\_\+thickness
\item 
\mbox{\Hypertarget{graph_8h_aa2936ecd84787e1d190c651258baaf61}\label{graph_8h_aa2936ecd84787e1d190c651258baaf61}} 
\hyperlink{structCell}{Cell} {\bfseries maze} \mbox{[}10\mbox{]}\mbox{[}10\mbox{]} = \{ \hyperlink{structCell}{Cell}\{ 0, \{ 0 \}, false \} \}
\item 
\mbox{\Hypertarget{graph_8h_af1d3cff2e4538e23400e260bae3dadad}\label{graph_8h_af1d3cff2e4538e23400e260bae3dadad}} 
int {\bfseries row} = 0
\item 
\mbox{\Hypertarget{graph_8h_afb52e720f5f0c483db5861f9e42e924e}\label{graph_8h_afb52e720f5f0c483db5861f9e42e924e}} 
int {\bfseries col} = 0
\item 
\mbox{\Hypertarget{graph_8h_a58d94fa8f7ddf189cd6eabdea4f2346c}\label{graph_8h_a58d94fa8f7ddf189cd6eabdea4f2346c}} 
\hyperlink{util_8h_a92e22a126ad6bf9d255b517e70d083f6}{Direction} {\bfseries dir} = Direction\+::\+East
\end{DoxyCompactItemize}

\subsection{Detailed Description}
Contains the structure of the maze and functions to alter the robot\textquotesingle{}s relation to the grid. 

\subsection{Function Documentation}
\mbox{\Hypertarget{graph_8h_ab4afdc4009e71e9811133449a48262c6}\label{graph_8h_ab4afdc4009e71e9811133449a48262c6}} 
\index{graph.\+h@{graph.\+h}!get\+Relative\+Heading@{get\+Relative\+Heading}}
\index{get\+Relative\+Heading@{get\+Relative\+Heading}!graph.\+h@{graph.\+h}}
\subsubsection{\texorpdfstring{get\+Relative\+Heading()}{getRelativeHeading()}}
{\footnotesize\ttfamily \hyperlink{util_8h_a92e22a126ad6bf9d255b517e70d083f6}{Direction} get\+Relative\+Heading (\begin{DoxyParamCaption}\item[{int}]{offset }\end{DoxyParamCaption})}

This gets the cardinal direction relative to the robot\textquotesingle{}s current heading offset = 0 =$>$ the direction the robot is facing offset = 1 =$>$ the direction to the robot\textquotesingle{}s left offset = -\/1 =$>$ the direction to the robot\textquotesingle{}s right offset = 2 =$>$ the direction behind the robot etc.

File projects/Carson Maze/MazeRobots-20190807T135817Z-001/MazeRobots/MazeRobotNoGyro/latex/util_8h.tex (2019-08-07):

\hypertarget{util_8h}{}\section{P\+C\+B\+\_\+test/\+P\+C\+B\+\_\+test/util.h File Reference}
\label{util_8h}\index{P\+C\+B\+\_\+test/\+P\+C\+B\+\_\+test/util.\+h@{P\+C\+B\+\_\+test/\+P\+C\+B\+\_\+test/util.\+h}}

Contains a variety of miscellaneous math functions to allow for cleaner code.  

This graph shows which files directly or indirectly include this file\+:
\nopagebreak
\begin{figure}[H]
\begin{center}
\leavevmode

\end{center}
\end{figure}
\subsection*{Enumerations}
\begin{DoxyCompactItemize}
\item 
enum \hyperlink{util_8h_a92e22a126ad6bf9d255b517e70d083f6}{Direction} \+: byte \{ {\bfseries East} = (1 $<$$<$ 0), 
{\bfseries North} = (1 $<$$<$ 1), 
{\bfseries West} = (1 $<$$<$ 2), 
{\bfseries South} = (1 $<$$<$ 3)
 \}\begin{DoxyCompactList}\small\item\em Represents all directions in the maze. \end{DoxyCompactList}
\end{DoxyCompactItemize}
\subsection*{Functions}
\begin{DoxyCompactItemize}
\item 
\mbox{\Hypertarget{util_8h_ab3bf9f71e060eb5fe4c94a7c13eacc5a}\label{util_8h_ab3bf9f71e060eb5fe4c94a7c13eacc5a}} 
{\footnotesize template$<$typename T $>$ }\\T \hyperlink{util_8h_ab3bf9f71e060eb5fe4c94a7c13eacc5a}{signum} (const T \&value)
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

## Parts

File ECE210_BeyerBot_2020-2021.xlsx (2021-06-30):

Part | Price ea | Qnty | Cost | Link | Required | Have | Need | Total Cost
TT Motor | $2.36 | 2.00 | $4.72 | https://www.adafruit.com/product/3777 | 140 | 95 | 45 | $106.20
3.3V 250mA Linear Voltage Regulator - L4931 | $0.86 | 1.00 | $0.86 | https://www.adafruit.com/product/2166 | 70 | 4 | 66 | $56.76
Breadboard | $8.99 | 0.17 | $1.50 | https://www.amazon.com/DEYUE-breadboard-Set-Prototype-Board/dp/B07LFD4LT6 | 40 | 40 | 0 | $0.00
Velcro (pack of 100) | $7.99 | 0.02 | $0.13 | https://www.amazon.com/Cable-Ties-Management-Microfiber-Adjustable/dp/B07H6BPYRB | 1 | 0 | 1 | $7.99
Arduino uno kit | $22.00 | 1.00 | $20.90 | https://www.amazon.com/Arduino-A000066-ARDUINO-UNO-R3/dp/B008GRTSV6?s=electronics | 70 | 37 | 33 | $726.00
Elegoo Wire Kit | $6.98 | 1.00 | $6.98 | https://www.amazon.com/Elegoo-EL-CP-004-Multicolored-Breadboard-arduino/dp/B01EV70C78 | 20 | 12 | 8 | $55.84
Photoresistor | $5.78 | 0.15 | $0.87 | https://www.amazon.com/Gikfun-Photoresistor-GL5516-Resistors-Arduino/dp/B00RLGFIEY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 |  |  | 0 | $0.00
PCB board | $0.70 | 1.00 | $0.70 | order from pcbway or JLC, assume quantity 100 | 70 | 70 | 0 | $0.00
battery 8.4V, 900 mAhr NiMH AAA cells | $11.66 | 1.00 | $11.66 | https://www.pololu.com/product/2236 |  |  | 0 | $0.00
Motor Driver: TB6612 | $2.94 | 1.00 | $2.94 | https://www.pololu.com/product/713 | 70 | 4 | 66 | $194.04
Sharp IR Sensors: GP2Y0A51SK0F | $9.93 | 3.00 | $29.79 | https://www.pololu.com/product/2450 | 210 | 126 | 84 | $834.12
IR Sensor wires | $0.79 | 3.00 | $2.37 | https://www.pololu.com/product/2411 | 210 | 22 | 188 | $148.52
QTR-8RC Reflectance Sensor Array | $7.95 | 1.00 | $7.95 | https://www.pololu.com/product/961 | 70 | 40 | 30 | $238.50
Phillips Screwdriver | $1.35 | 1.00 | $1.35 | https://www.pololu.com/product/158 | 30 | 30 | 0 | $0.00
5V TO-220 L7805ACV Regulator | $0.47 | 1.00 | $0.47 | https://www.mouser.com/ProductDetail/STMicroelectronics/L7805ACV | 70 | 6 | 64 | $30.08
Bipolar Transistors - BJT NPN - 2N3904TAR | $0.06 | 2.00 | $0.12 | https://www.mouser.com/ProductDetail/ON-Semiconductor-Fairchild/2N3904TAR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 | 140 | 10 | 130 | $7.67
PNP Transistor - 2N3906 | $0.06 | 1.00 | $0.06 | https://www.mouser.com/ProductDetail/ON-Semiconductor-Fairchild/2N3906TF | 80 | 80 | 0 | $0.00
Male to female #4-40 standoffs 2" | $0.57 | 4.00 | $2.28 | https://www.mouser.com/ProductDetail/Fascomp/FC4558-440-A?qs=sGAEpiMZZMtrde5aJd3qw6rAysW6QWVksr2cJwjPrqU%3D | 400 | 300 | 100 | $57.00
Female to female #4-40 standoffs 1" | $0.26 | 4.00 | $1.04 | https://www.mouser.com/ProductDetail/Fascomp/FC2112-440-A?qs=sGAEpiMZZMtrde5aJd3qw7vH8KtW0Jf63LChwDms0E0%3D | 400 | 200 | 200 | $52.00
Toggle switch | $1.59 | 1.00 | $1.59 | https://www.jameco.com/z/DS-40T1B1A1-1-Toggle-Switch-Single-Pole-Single-Throw-ON-OFF-SMTS101-Solder-3A-120-Amp-7-32-Inch-Mounting_72161.html | 70 | 8 | 62 | $98.58
10uF electrolytic | $0.11 | 1.00 | $0.11 | https://www.jameco.com/webapp/wcs/stores/servlet/ProductDisplay?catalogId=10001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 | 210 | 85 | 125 | $13.75
33uF electrolytic | $0.08 | 1.00 | $0.08 | https://www.jameco.com/z/R33-50-VP-R-Capacitor-Radial-33-uF-50-Volt-20-85c-6-3x11x2-5mm_93747.html | 160 | 50 | 110 | $8.80
0.1uF non-polarized | $0.08 | 3.00 | $0.24 | https://www.jameco.com/z/DC-1-25-Capacitor-Ceramic-Disc-0-1-micro-F-25V-plusmn-20-37-_151116.html | 210 | 20 | 190 | $15.20
10k 1/4W resistor | $0.02 | 5.00 | $0.09 | https://www.jameco.com/z/CF1-4W103JRC-Resistor-Carbon-Film-10k-Ohm-1-4-Watt-5-_691104.html | 350 | 30 | 320 | $5.73
330 1/4W resistor | $0.02 | 1.00 | $0.02 | https://www.jameco.com/z/CF1-4W331JRC-Resistor-Carbon-Film-330-Ohm-1-4-Watt-5-_690742.html | 200 | 70 | 130 | $2.33
13k resistor | $0.02 | 1.00 | $0.02 | https://www.jameco.com/z/CF1-4W133JRC-Resistor-Carbon-Film-13K-Ohm-1-4-Watt-5-_691139.html | 200 | 54 | 146 | $2.61
1K resistor | $0.02 | 1.00 | $0.02 | https://www.jameco.com/z/CF1-4W102JRC-Resistor-Carbon-Film-1k-Ohm-1-4-Watt-5-_690865.html | 200 | 10 | 190 | $3.40
LED 5mm | $4.95 | 0.02 | $0.10 | https://www.jameco.com/z/GB110R-100-Piece-Red-LED-Grab-Bag_2226943.html | 2 | 1 | 1 | $4.95
Male 1x24 | $0.30 | 1.00 | $0.30 | https://www.peconnectors.com/pin-headers-straight-1x-row-.100/hws1646/ | 70 | 50 | 20 | $6.00
Female 1x8 header | $0.40 | 2.00 | $0.80 | https://www.peconnectors.com/female-headers-pcb-1x-row-.100/hws1362/ | 140 | 50 | 90 | $36.00
Female 2x5 header | $0.49 | 1.00 | $0.49 | https://www.peconnectors.com/female-headers-pcb-2x-row-.100/hws1020/ | 70 | 70 | 0 | $0.00
Female 1x2 header | $0.30 | 2.00 | $0.60 | https://www.peconnectors.com/female-headers-pcb-1x-row-.100/hws15768/ | 140 | 40 | 100 | $30.00
Line sensor 90 deg header 1x40 | $0.67 | 1.00 | $0.67 | https://www.peconnectors.com/pin-headers-r/a-1x-row-.100/hws15655/ | 70 | 70 | 0 | $0.00
#4-40 x 1" Screw | $0.10 | 6.00 | $0.60 | https://www.fastenal.com/product?query=72494&fsi=1 | 600 | 400 | 200 | $20.00
#4-40 x 1/4" Screw | $0.05 | 8.00 | $0.40 | https://www.fastenal.com/product?query=1172478&fsi=1 | 800 | 700 | 100 | $5.00
#2-56 X 1/4" Screw | $0.04 | 10.00 | $0.40 | https://www.fastenal.com/product?query=72456&fsi=1 | 1000 | 700 | 300 | $12.00
#2-56 X 1/2" Screw | $0.06 | 10.00 | $0.60 | https://www.fastenal.com/products/details/72464 (https://www.fastenal.com/product?query=72456&fsi=1) | 1000 | 700 | 300 | $18.00
#4-40 Nut | $0.08 | 6.00 | $0.48 | https://www.fastenal.com/product?query=70704&fsi=1 | 600 | 400 | 200 | $16.00
#2-56 Nut | $0.07 | 8.00 | $0.56 | https://www.fastenal.com/product?query=70702&fsi=1 | 800 | 500 | 300 | $21.00
Total Cost Per Bot: |  |  | $104.85 |  | Cadets: | 100 | Total: | $2834.07

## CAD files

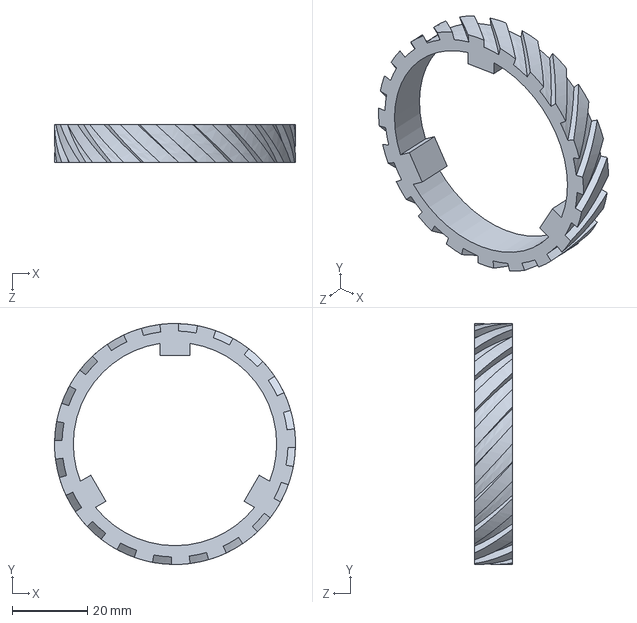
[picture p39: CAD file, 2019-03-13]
3D_Printing/solid works/Ninja_Flex_Tire - left.SLDPRT
64.0 x 64.0 x 10.0 mm

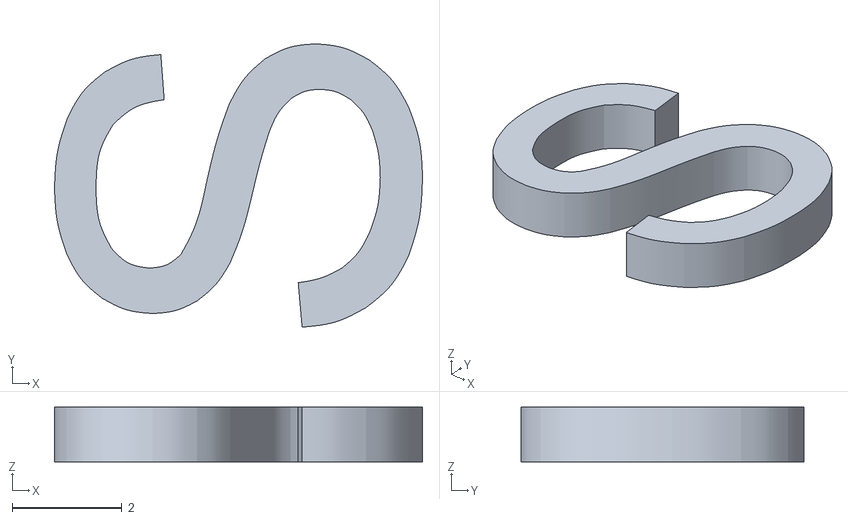
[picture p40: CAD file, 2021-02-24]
3D_Printing/stl/MultiColorNameplate/Body45.stl
6.72 x 5.17 x 1.00

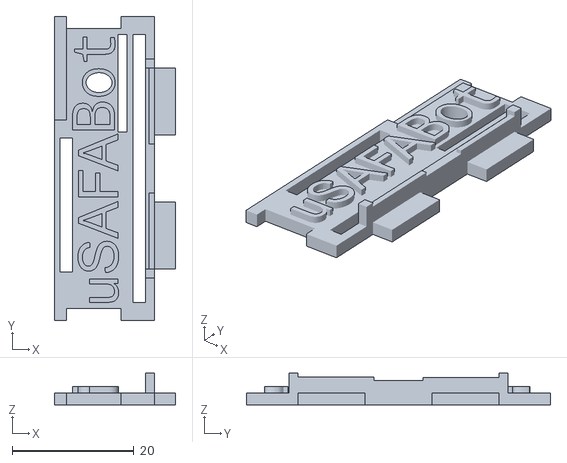
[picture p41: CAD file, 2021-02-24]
3D_Printing/stl/Nameplate2.stl
20.0 x 50.0 x 5.25

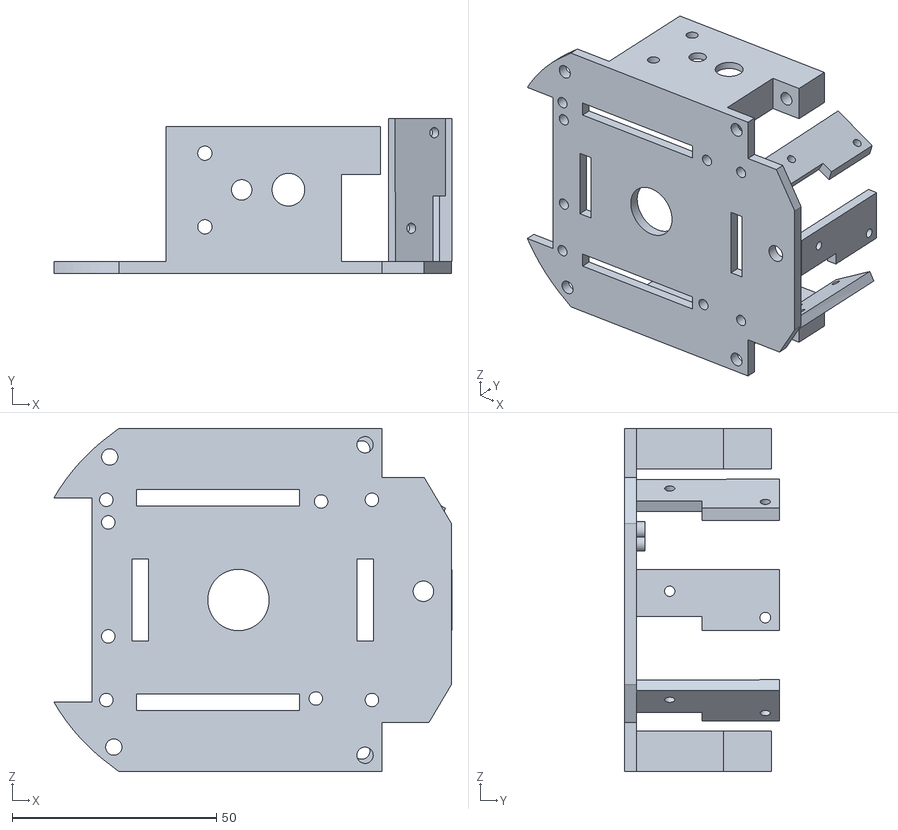
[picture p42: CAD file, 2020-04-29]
3D_Printing/stl/Version3/MotorLayer.stl
97.4 x 38.0 x 84.0

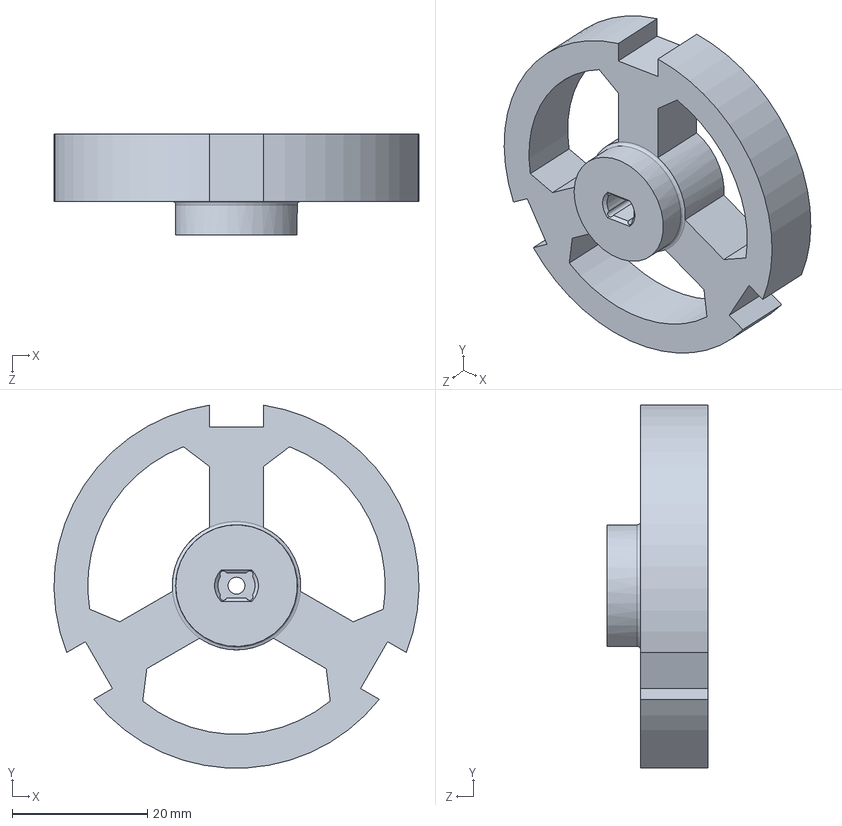
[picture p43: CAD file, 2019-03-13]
3D_Printing/solid works/rim.sldprt
54.0 x 53.7 x 15.0 mm

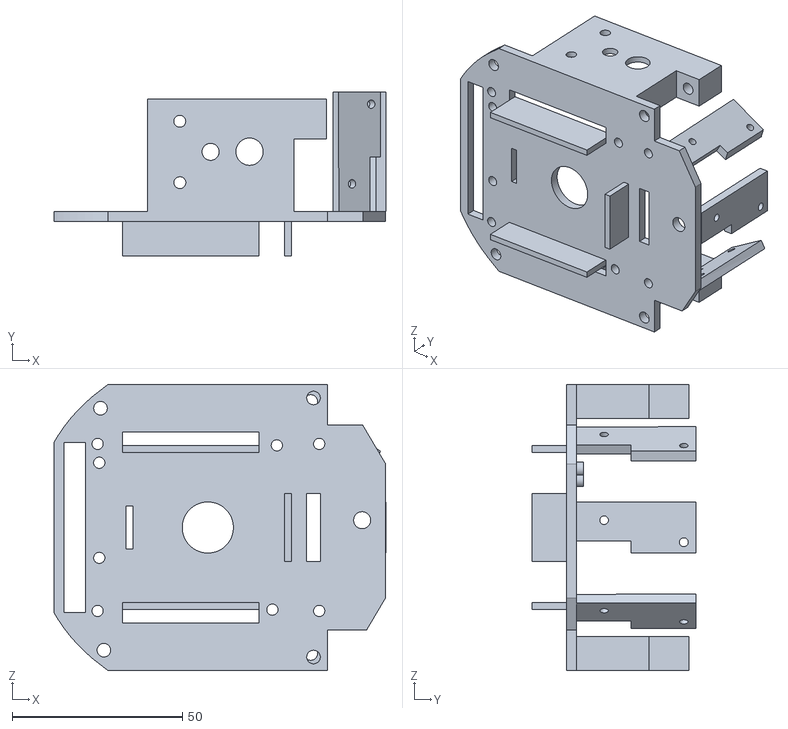
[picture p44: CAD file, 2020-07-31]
3D_Printing/stl/MotorLayer_experiment.stl
97.4 x 48.0 x 84.0

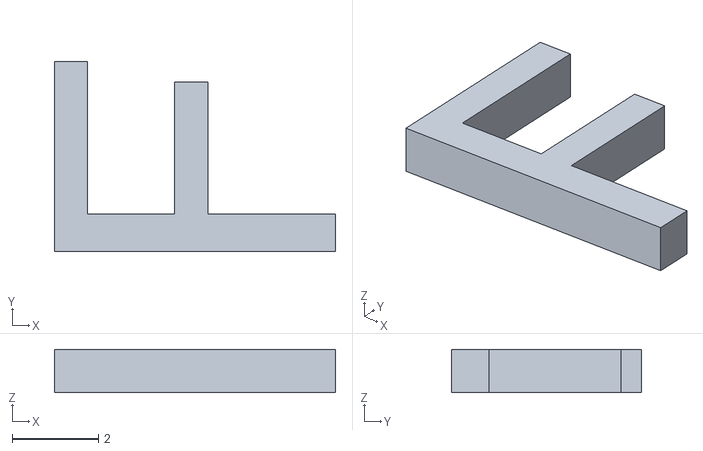
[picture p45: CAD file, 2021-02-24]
3D_Printing/stl/MultiColorNameplate/Body46.stl
6.50 x 4.39 x 1.00

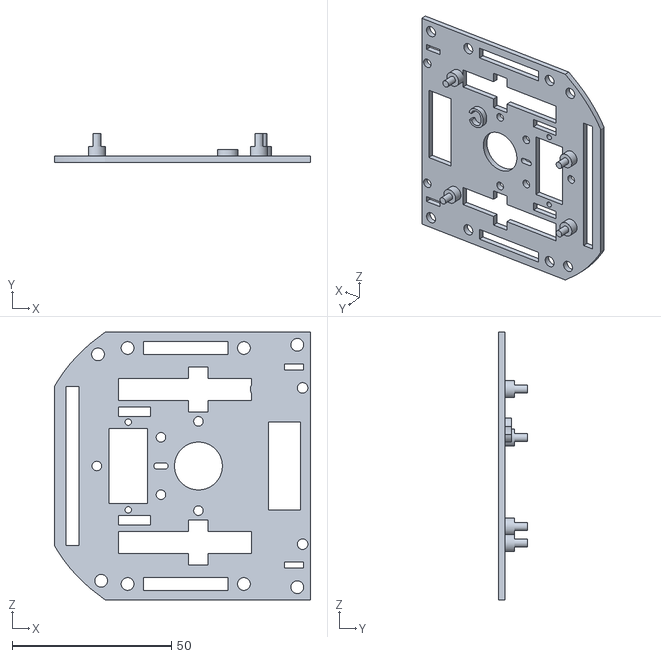
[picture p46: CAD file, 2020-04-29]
3D_Printing/stl/Version3/ArduinoLayer.stl
80.3 x 9.00 x 84.0

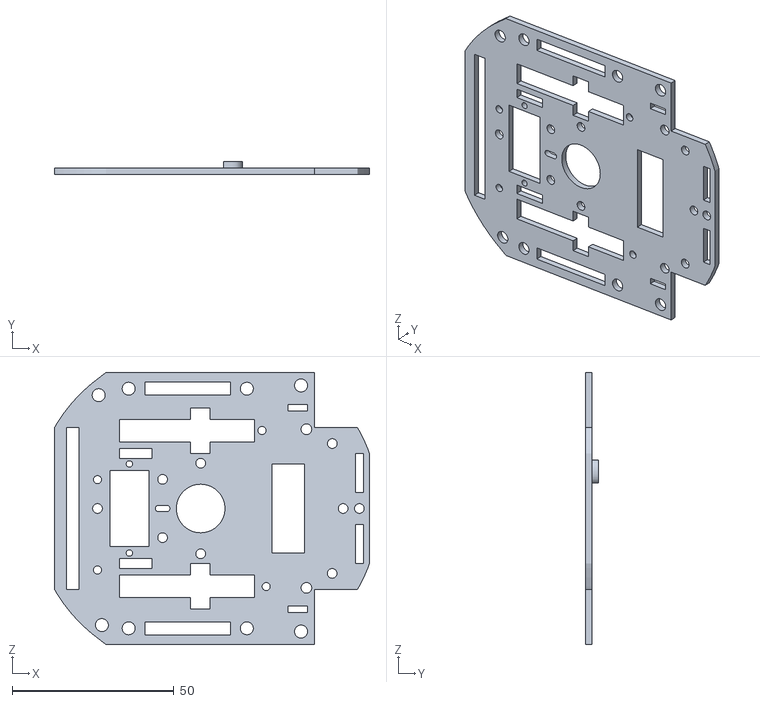
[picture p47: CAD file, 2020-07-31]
3D_Printing/stl/Layer.stl
97.3 x 4.00 x 84.0

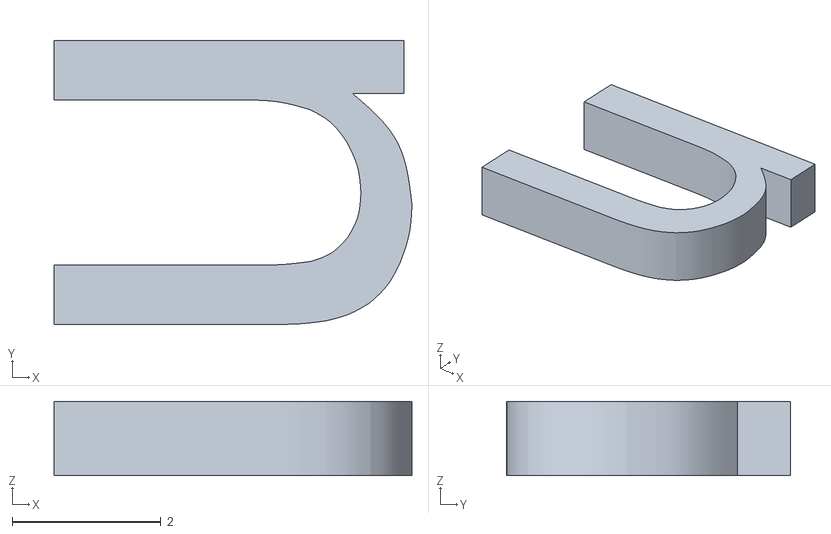
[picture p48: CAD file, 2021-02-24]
3D_Printing/stl/MultiColorNameplate/Body47.stl
4.82 x 3.82 x 1.00

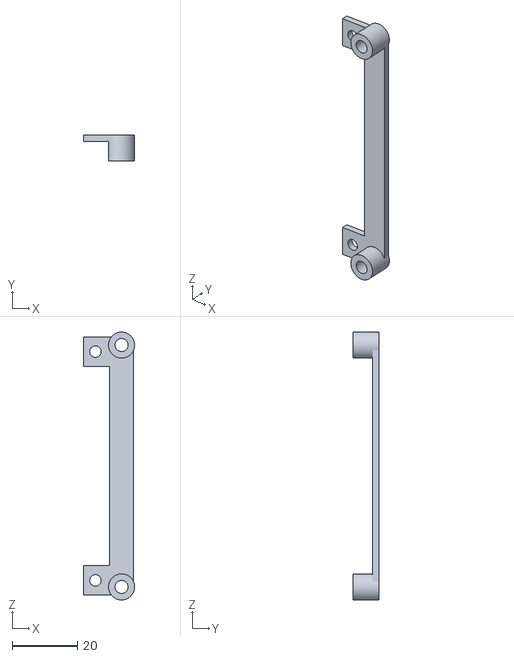
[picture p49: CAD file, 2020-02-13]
3D_Printing/stl/Version3/LineSensorMount.stl
15.7 x 8.00 x 82.0

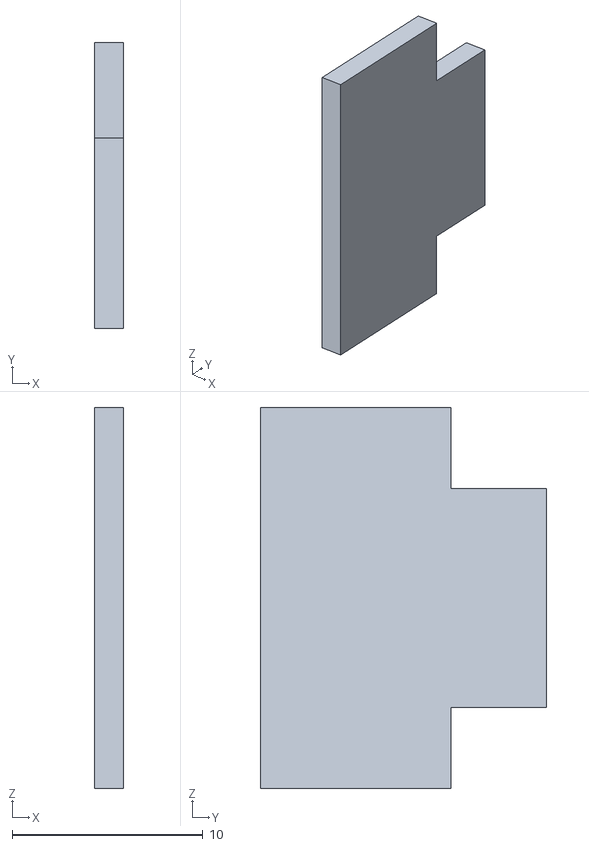
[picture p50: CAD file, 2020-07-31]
3D_Printing/stl/BatteryGuard.stl
1.50 x 15.0 x 20.0

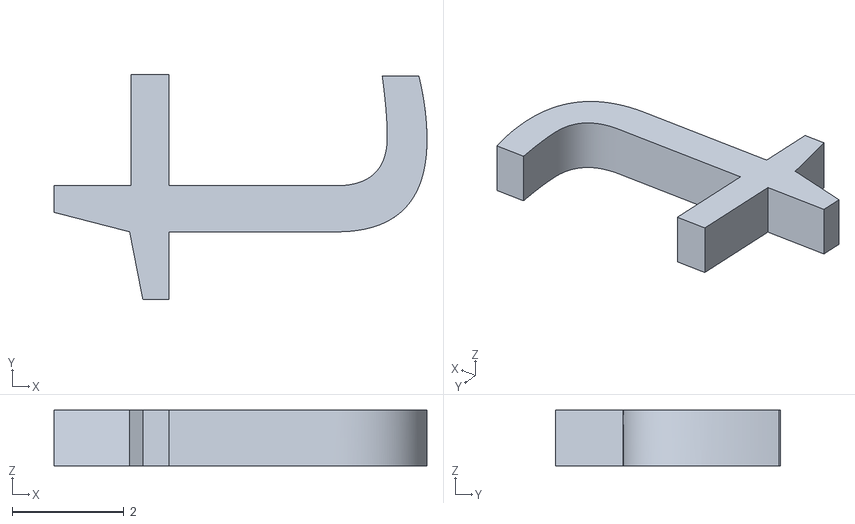
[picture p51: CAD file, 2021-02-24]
3D_Printing/stl/MultiColorNameplate/Body44.stl
6.67 x 4.03 x 1.00

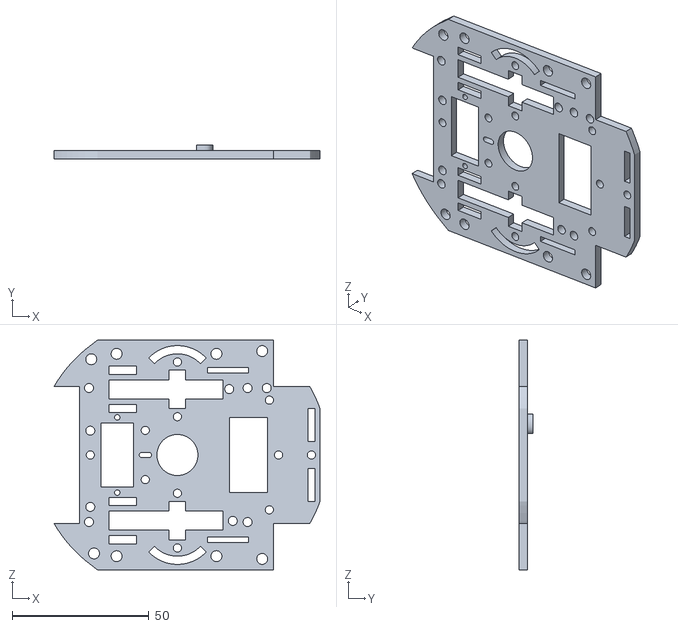
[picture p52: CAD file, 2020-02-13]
3D_Printing/stl/Version3/Layer.stl
97.3 x 5.00 x 84.0

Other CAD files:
3D_Printing/solid works/Ninja_Flex_Tire - right.SLDPRT
3D_Printing/stl/MotorLayer1.stl
3D_Printing/stl/MultiColorNameplate/Body27.stl
3D_Printing/stl/Version3/BaseLayer.stl
3D_Printing/fusion/Archive/Version1/ArduinoLayer.f3d
3D_Printing/fusion/Archive/Version1/BaseLayer.f3d
3D_Printing/fusion/Archive/Version1/Layer.f3d
3D_Printing/fusion/Archive/Version1/MotorLayer.f3d
3D_Printing/fusion/Archive/Version2/ArduinoLayer.f3d
3D_Printing/fusion/Archive/Version2/BaseLayer.f3d
3D_Printing/fusion/Archive/Version2/Layer.f3d
3D_Printing/fusion/Archive/Version2/MotorLayer.f3d
3D_Printing/fusion/ArduinoLayer.f3d
3D_Printing/fusion/BaseLayer.f3d
3D_Printing/fusion/Layer.f3d
3D_Printing/fusion/MotorLayer.f3d
3D_Printing/fusion/Version2/ArduinoLayer.f3d
3D_Printing/fusion/Version2/BaseLayer.f3d
3D_Printing/fusion/Version2/Layer.f3d
3D_Printing/fusion/Version2/MotorLayer.f3d
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

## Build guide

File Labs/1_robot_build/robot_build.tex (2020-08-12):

\documentclass{handout}

%\SetInstructor{Capt Steven Beyer}
\SetCourseTitle{ECE210: Introduction to Electrical and Computer Engineering}
\SetHandoutTitle{Build Robot}

%\ShowAllBlanks

\usepackage[obeyspaces]{url}

\graphicspath{{./figs/}}

%\showsoln \setsolncolor{red}

\begin{document}
	%	\footnotetext{Examples are abstracted from Tutorials Point, "Arduino", 2019, accessed Feb 18, 2019. [Online]. Available: https://www.tutorialspoint.com/arduino/index.htm}
	\maketitle
	\begin{figure}[H]
		\centering
		
	\end{figure}
	
	\section{Objectives.} 
	\begin{enumerate}
		\item Demonstrate the ability to build a robotics system using Electrical and Computer Engineering (ECE) fundamentals such as soldering, assembly, and fabrication.
		\item Troubleshoot ECE applications utilizing modern test equipment.
	\end{enumerate}
	
	\section{Materials.}
	\begin{minipage}{.5\textwidth}
	\begin{enumerate}
		\item Soldered Printed Circuit Board (PCB)
		\item Arduino Uno
		\item 3D-printed structural pieces (A-D)
		\item 2 - DC motors
		\item 2 - wheels
		\item 2 - tires (note left and right are different)
		\item 1 - Battery pack
		\item Jumper wire pack
		\item 1 - Switch
		\item 3 - IR sensors
		\item 1 - QTR-8RC Reflectance Sensor Array

		\item 1 - 1x11 90$^o$ header
			\end{enumerate}
\end{minipage}\hfill
\begin{minipage}{.5\textwidth}
\begin{enumerate}
		\item 8 - hex standoffs (4 short and 4 long)
		\item Bolts
		\begin{enumerate}
			\item 6 - \# 4-40 x 1"
			\begin{enumerate}
				\item 4 for motors
				\item 2 for connecting A and B
			\end{enumerate}
			\item 8 - \# 4-40 x 1/4"
			\begin{enumerate}
				\item 8 for connecting standoffs to layers
			\end{enumerate}
			\item 10 - \# 2-56 x 1/4"
			\begin{enumerate}
				\item 2 for line sensors
				\item 6 for IR sensors
				\item 2 for wheels
			\end{enumerate}
		\end{enumerate}
		\item Nuts
		\begin{enumerate}
			\item 6 - \# 4-40
			\item 8 - \# 2-56
		\end{enumerate}
	\end{enumerate}
\end{minipage}
	\newpage
\clearpage
\pagebreak
	
	\section{Layer A - Base Layer.}
	\begin{enumerate}
		\item Remove the support from Layer A.
		\item Place the PCB on the printed spacers with the ``Beyer" printed text towards the rounded edge.
		
		\begin{figure} [H]
			\centering
			
		\end{figure}
	
		\item Solder the 1 x 11 90$^o$ header to the reflectance sensor array with the header opposite of the line sensors
		
		\item Solder a jumper across the $3.3\ V$ bypass.
		
		\item Secure the reflectance sensor array to the line sensor mount using 2 - \#2-56 x 1/4" bolts and nuts.
		
		\begin{figure} [H]
			\centering
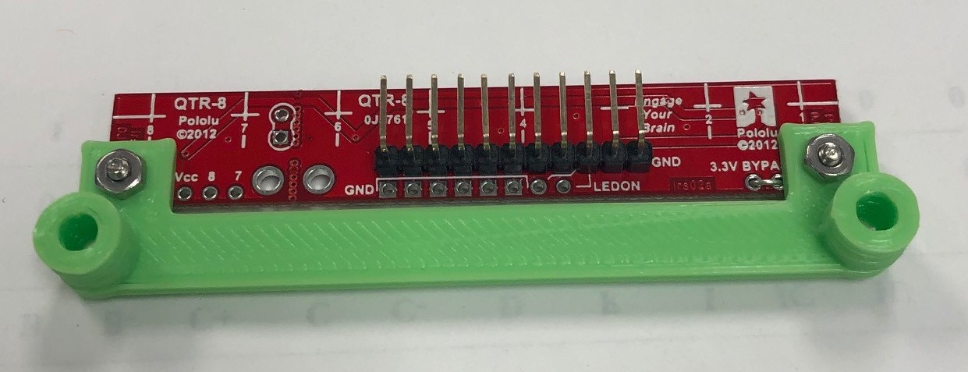
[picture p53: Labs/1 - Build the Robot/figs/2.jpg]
			
		\end{figure}
	\end{enumerate}
	
	\section{Layer B - Motor Layer.}
	\begin{enumerate}
		\item Remove the support from Layer B.
		\item Use 4 - \# 4-40 x 1/4" bolts and attach the 4 short hex standoffs to Layer B (outermost holes and opposite of the printed B).
		\item Install the 2 DC motors to Layer B with wires facing inwards. The motors have yellow plastic cases that should be oriented towards the front of Layer B. The white plastic drive shafts should be protruding through the side holes of Layer B. Use 4 - \# 4-40 x 1" bolts and nuts to secure each motor (Ensure the screw heads are to the outside of Layer B).
		
		\begin{figure} [H]
			\centering
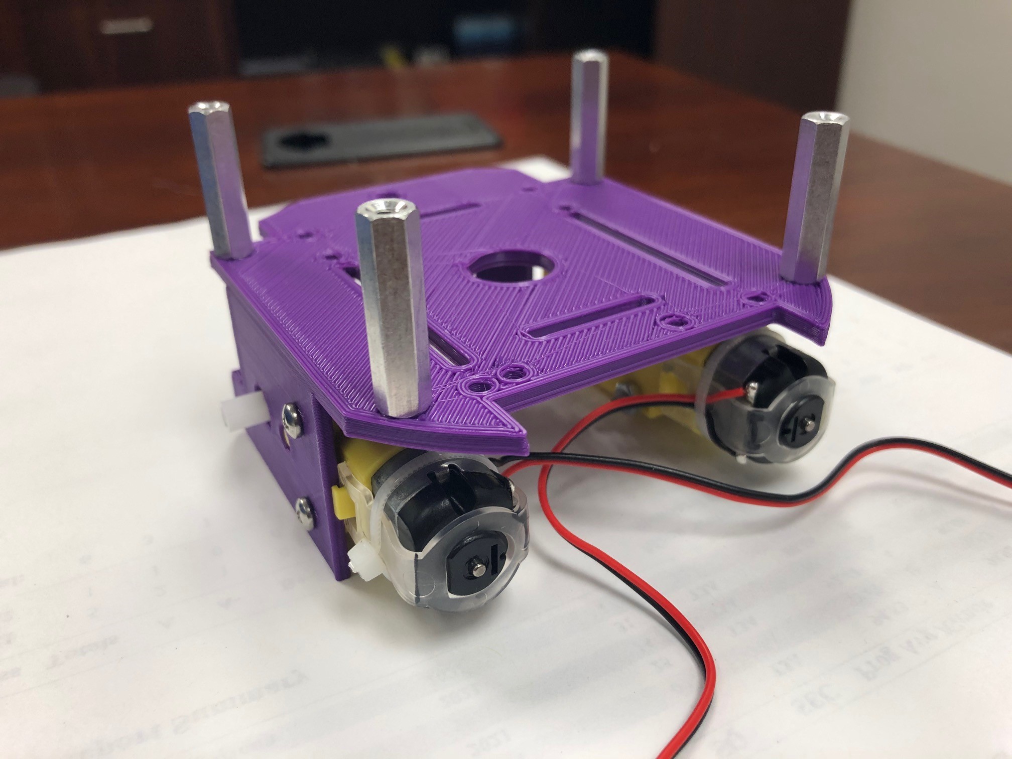
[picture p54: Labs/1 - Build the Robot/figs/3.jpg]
			
		\end{figure}
		
		\item \textbf{IR Sensor:} Connect three IR sensors to the sensor mounts on the front of the bot using 6 - \#2-56 x 1/4" bolts and nuts.

		\item Solder three JST IR Sensor cables:
		\begin{itemize}
			\item Solder the three black wires to a single black jumper wire.
			\item Solder the three red wires to a single red jumper wire.
			\item Solder the left IR Sensor's yellow wire to a single green jumper wire.
			\item Solder the center IR Sensor's yellow wire to a single yellow jumper wire.
			\item Solder the right IR Sensor's yellow wire to a single orange jumper wire.
		\end{itemize}
	
		\item \textbf{Switch:} Solder the male ends of two male-to-female jumper wires to the connectors on the switch.
		\item Remove the two nuts and lock washer that came attached to the switch and use one nut to attach it to Layer B in the same direction as the standoffs.
		
		\item \textbf{Wheels:} Attach the wheels by sliding them onto the axles. Use 2 - \# 2-56 x 1/4" bolts to secure the wheels onto the axles.
		
		\begin{figure} [H]
			\centering
			
		\end{figure}
		
		\item \textbf{Battery:} Connect a male to female jumper to the \textit{BATT} headers on the PCB and feed through a slot in Layer B. These wires will connect to the battery and enable the removal of the battery without taking apart the bot.
		
		\begin{figure} [H]
			\centering
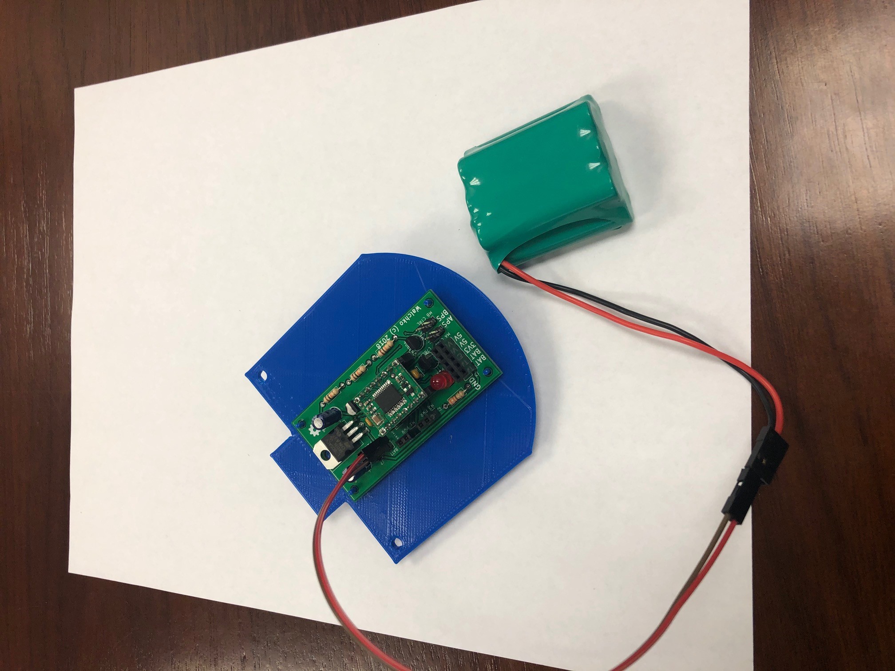
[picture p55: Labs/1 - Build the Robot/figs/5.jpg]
			
		\end{figure}
		
		\item \textbf{Testing PCB:} Wire the motors, Arduino, battery, and switch to the PCB as shown in Figure. Download the \path{robot_pcb} folder from \textbf{Teams} (\path{Labs/robot_pcb}). Copy the Motor library from \textbf{Teams} (\path{Labs/Custom Libraries/Motor}) to your documents folder: \\\path{Documents/Arduino/libraries/} Open the \path{robot_pcb.ino} file. Compile and upload to the Arduino. If working correctly, the tires should go forward for 1 second, then left for 1 second, then right for 1 second, then backwards for 1 second. Disconnect the PCB from the Arduino.
		
		\begin{figure} [H]
			\centering
			
		\end{figure}
		
		\item Secure the battery to Layer B using velcro.
		
		\begin{figure} [H]
			\centering
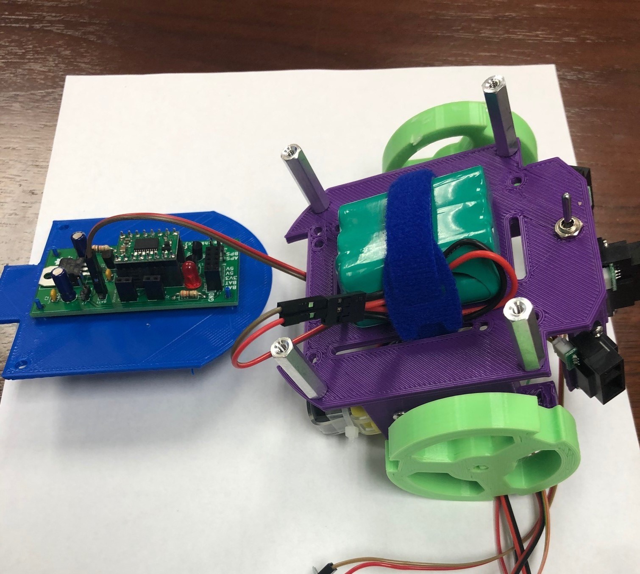
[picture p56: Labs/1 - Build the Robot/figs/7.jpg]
			
		\end{figure}
		
	\end{enumerate}

	\section{Layer C - Arduino Layer.}
	\begin{enumerate}
		\item Connect Layer C to Layer B using the larger standoffs.
		\item Place the Arduino on the printed spacers (will only go one direction).
		\item Wire the Arduino to the PCB going through the slots in Layer C and B.
		\item Feed the wires from the IR sensors through the slots at the front of Layer B and C.
		
		\begin{figure} [H]
			\centering
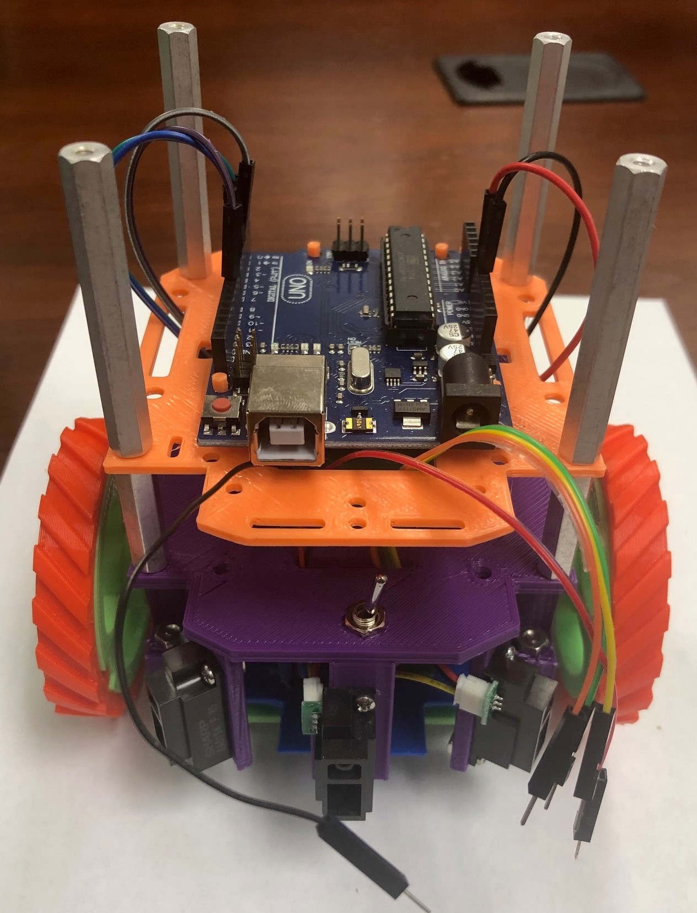
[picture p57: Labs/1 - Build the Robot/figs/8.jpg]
			
		\end{figure}

	\end{enumerate}

	\section{Connect Layer A to Layer B/C.}
	\begin{enumerate}
		\item Connect the three layers using the line sensor mount and 2 - \# 4-40 x 1" bolts and nuts.
		
		\begin{figure} [H]
			\centering
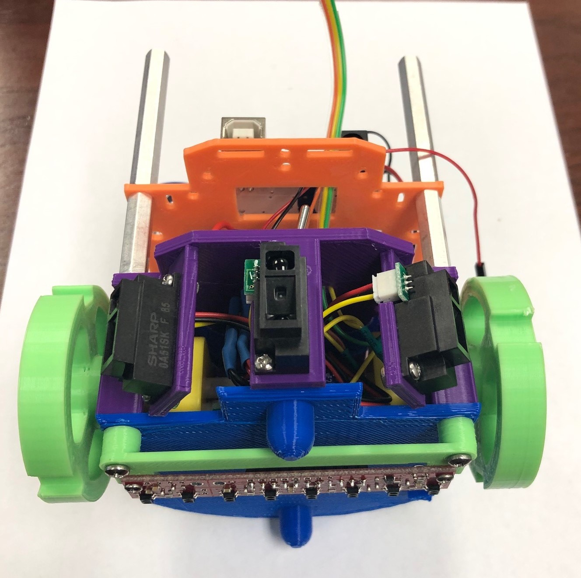
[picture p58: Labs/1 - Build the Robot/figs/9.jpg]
			
		\end{figure}
		
		\item Put the tires on the wheels.
		
		\begin{figure} [H]
			\centering
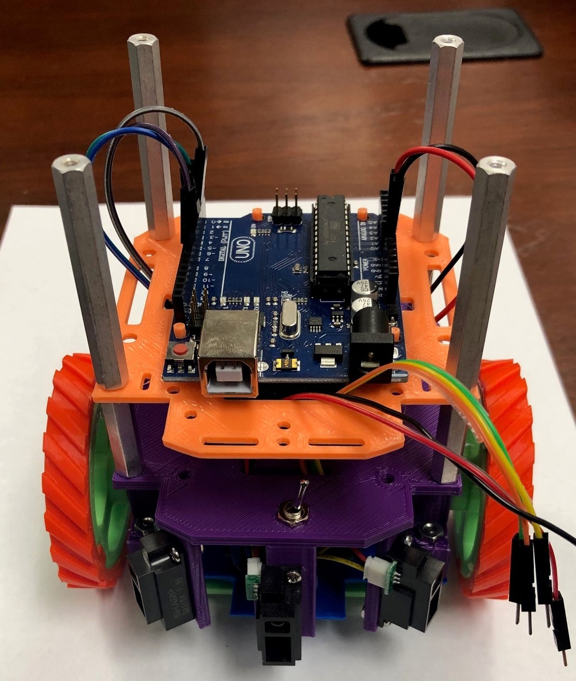
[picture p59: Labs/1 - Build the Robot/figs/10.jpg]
			
		\end{figure}
		
	\end{enumerate}

	\section{Testing.}
	\begin{enumerate}
		\item Connect the battery to the jumper and turn on the PCB. The robot should drive in the same pattern as before.
	\end{enumerate}

	\newpage
	\clearpage
	\pagebreak
	
\end{document}

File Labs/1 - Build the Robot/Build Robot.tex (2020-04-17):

\documentclass{handout}

%\SetInstructor{Capt Steven Beyer}
\SetCourseTitle{ECE210: Introduction to Electrical and Computer Engineering}
\SetHandoutTitle{Build BeyerBot}

%\ShowAllBlanks

\usepackage[obeyspaces]{url}

\graphicspath{{./figs/}}

%\showsoln \setsolncolor{red}

\begin{document}
	%	\footnotetext{Examples are abstracted from Tutorials Point, "Arduino", 2019, accessed Feb 18, 2019. [Online]. Available: https://www.tutorialspoint.com/arduino/index.htm}
	\maketitle
	
	\section{Objectives.} 
	\begin{enumerate}
		\item Demonstrate the ability to build a robotics system using Electrical and Computer Engineering (ECE) fundamentals such as soldering, assembly, and fabrication.
		\item Troubleshoot ECE applications utilizing modern test equipment.
	\end{enumerate}
	
	\section{Materials.}
	\begin{enumerate}
		\item Soldered Printed Circuit Board (PCB)
		\item Arduino Uno
		\item 3D-printed structural pieces (A-D)
		\item 2 DC motors
		\item 2 wheels
		\item 2 tires (note left and right are different)
		\item Battery pack
		\item Jumper wires
		\item Switch
		\item 3 IR sensors
		\item 1 QTR-8RC Reflectance Sensor Array
		\item 1 1 x 11 90$^o$ header
		\item 8 hex standoffs (4 short and 4 long)
		\item Bolts
		\begin{enumerate}
			\item 6 - \# 4-40 x 1"
			\begin{enumerate}
				\item 4 for motors
				\item 2 for connecting A and B
			\end{enumerate}
			\item 8 - \# 4-40 x 1/4"
			\begin{enumerate}
				\item 8 for connecting standoffs to layers
			\end{enumerate}
			\item 10 - \# 2-56 x 1/4"
			\begin{enumerate}
				\item 2 for line sensors
				\item 6 for IR sensors
				\item 2 for wheels
			\end{enumerate}
		\end{enumerate}
		\item Nuts
		\begin{enumerate}
			\item 6 - \# 4-40
			\item 8 - \# 2-56
		\end{enumerate}
	\end{enumerate}
	\newpage
\clearpage
\pagebreak
	
	\section{Layer A - Base Layer.}
	\begin{enumerate}
		\item Remove the support from Layer A.
		\item Place the PCB on the printed spacers with the ``Walchko" printed text towards the rounded edge.
		
		\begin{figure} [H]
			\centering
			
		\end{figure}
	
		\item Solder the 1 x 11 90$^o$ header to the reflectance sensor array with the bent header opposite of the line sensors
		\item Secure the reflectance sensor array to the line sensor mount using 2 - \#2-56 x 1/4" bolts and nuts.
		
		\begin{figure} [H]
			\centering
			
		\end{figure}
	\end{enumerate}
	
	\section{Layer B - Motor Layer.}
	\begin{enumerate}
		\item Remove the support from Layer B.
		\item Use 4 - \# 4-40 x 1/4" bolts and attach the 4 short hex standoffs to Layer B (outermost holes and opposite of the printed B).
		\item Install the 2 DC motors to Layer B with wires facing inwards. The motors have yellow plastic cases that should be oriented towards the front of Layer B. The white plastic drive shafts should be protruding through the side holes of Layer B. Use 4 - \# 4-40 x 1" bolts and nuts to secure each motor (Ensure the screw heads are to the outside of Layer B).
		
		\begin{figure} [H]
			\centering
			
		\end{figure}
		
		\item \textbf{IR Sensor:} Connect three IR sensors to the sensor mounts on the front of the bot using 6 - \#2-56 x 1/4" bolts and nuts.
		\item \textbf{Switch:} Solder the male ends of two male-to-female jumper wires to the connectors on the switch.
		\item Remove the two nuts and lock washer that came attached to the switch and use one nut to attach it to Layer B in the same direction as the standoffs.
		
		\item \textbf{Wheels:} Attach the wheels by sliding them onto the axles. Use 2 - \# 2-56 x 1/4" bolts to secure the wheels onto the axles.
		
		\begin{figure} [H]
			\centering
			
		\end{figure}
		
		\item \textbf{Battery:} Connect a male to female jumper to the \textit{BATT} headers on the PCB and feed through a slot in Layer B. These wires will connect to the battery and enable the removal of the battery without taking apart the bot.
		
		\begin{figure} [H]
			\centering
			
		\end{figure}
		
		\item \textbf{Testing PCB:} Wire the motors, Arduino, battery, and switch to the PCB as shown in Figure. Download the \path{pcb\_test} folder from Canvas. Create the following folder:  \\\path{Program Files (x86)/Arduino/libraries/Motor} and move the \textit{Motor.h} file into it. Open the \textit{pcb\_test.ino} file. Compile and upload to the Arduino. If working correctly, the tires should go forward for 1 second, then left for 1 second, then right for 1 second, then backwards for 1 second. Disconnect the PCB from the Arduino.
		
		\begin{figure} [H]
			\centering
			
		\end{figure}
		
		\item Secure the battery to Layer B using velcro.
		
		\begin{figure} [H]
			\centering
			
		\end{figure}
		
	\end{enumerate}

	\section{Layer C - Arduino Layer.}
	\begin{enumerate}
		\item Connect Layer C to Layer B using the larger standoffs.
		\item Place the Arduino on the printed spacers (will only go one direction).
		\item Wire the Arduino to the PCB going through the slots in Layer C and B.
		\item Feed the wires from the IR sensors through the slots at the front of Layer B and C.
		
		\begin{figure} [H]
			\centering
			
		\end{figure}

	\end{enumerate}

	\section{Connect Layer A to Layer B/C.}
	\begin{enumerate}
		\item Connect the three layers using the line sensor mount and 2 - \# 4-40 x 1" bolts and nuts.
		
		\begin{figure} [H]
			\centering
			
		\end{figure}
		
		\item Put the tires on the wheels.
		
		\begin{figure} [H]
			\centering
			
		\end{figure}
		
	\end{enumerate}

	\section{Testing.}
	\begin{enumerate}
		\item Connect the battery to the jumper and turn on the PCB. The robot should drive in the same pattern as before.
	\end{enumerate}

	\newpage
	\clearpage
	\pagebreak
	
\end{document}

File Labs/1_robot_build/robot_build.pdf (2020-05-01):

ECE210: Introduction to Electrical and Computer Engineering

# Build Robot

1 Objectives.

1. Demonstrate the ability to build a robotics system using Electrical and Computer Engineering (ECE) fundamentals such as soldering, assembly, and fabrication.
2. Troubleshoot ECE applications utilizing modern test equipment.

2 Materials.

1. Soldered Printed Circuit Board (PCB)
2. Arduino Uno
3. 3D-printed structural pieces (A-D)
4. 2 - DC motors
5. 2 - wheels
6. 2 - tires (note left and right are different)
7. 1 - Battery pack
8. Jumper wire pack
9. 1 - Switch
10. 3 - IR sensors
11. 1 - QTR-8RC Reflectance Sensor Array
12. 1 - 1x11 90o header
13. 8 - hex standoffs (4 short and 4 long)
14. Bolts
(a) 6 - # 4-40 x 1”
i. 4 for motors
ii. 2 for connecting A and B
(b) 8 - # 4-40 x 1/4”
i. 8 for connecting standoffs to layers
(c) 10 - # 2-56 x 1/4”
i. 2 for line sensors
ii. 6 for IR sensors
iii. 2 for wheels
15. Nuts
(a) 6 - # 4-40
(b) 8 - # 2-56

ECE210: Introduction to Electrical and Computer Engineering -Build Robot

3 Layer A - Base Layer.

1. Remove the support from Layer A.
2. Place the PCB on the printed spacers with the “Beyer” printed text towards the rounded edge.

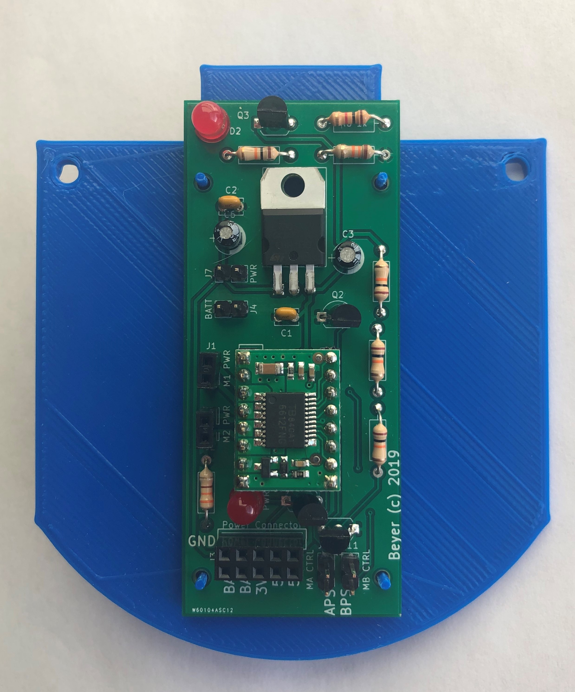
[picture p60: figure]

3. Solder the 1 x 11 90o header to the reflectance sensor array with the header opposite of the line sensors
4. Solder a jumper across the 3.3 V bypass.
5. Secure the reflectance sensor array to the line sensor mount using 2 - #2-56 x 1/4” bolts and nuts.


4 Layer B - Motor Layer.

1. Remove the support from Layer B.
2. Use 4 - # 4-40 x 1/4” bolts and attach the 4 short hex standoffs to Layer B (outermost holes and opposite of the printed B).
3. Install the 2 DC motors to Layer B with wires facing inwards. The motors have yellow plastic cases that should be oriented towards the front of Layer B. The white plastic drive shafts should be protruding through the side holes of Layer B. Use 4 - # 4-40 x 1” bolts and nuts to secure each motor (Ensure the screw heads are to the outside of Layer B).


4. IR Sensor: Connect three IR sensors to the sensor mounts on the front of the bot using 6 - #2-56 x 1/4” bolts and nuts.
5. Solder three JST IR Sensor cables:
| Solder the three black wires to a single black jumper wire.
| Solder the three red wires to a single red jumper wire.

| Solder the left IR Sensor’s yellow wire to a single green jumper wire.
| Solder the center IR Sensor’s yellow wire to a single yellow jumper wire.
| Solder the right IR Sensor’s yellow wire to a single orange jumper wire.
6. Switch: Solder the male ends of two male-to-female jumper wires to the connectors on the switch.
7. Remove the two nuts and lock washer that came attached to the switch and use one nut to attach it to Layer B in the same direction as the standoffs.
8. Wheels: Attach the wheels by sliding them onto the axles. Use 2 - # 2-56 x 1/4” bolts to secure the wheels onto the axles.

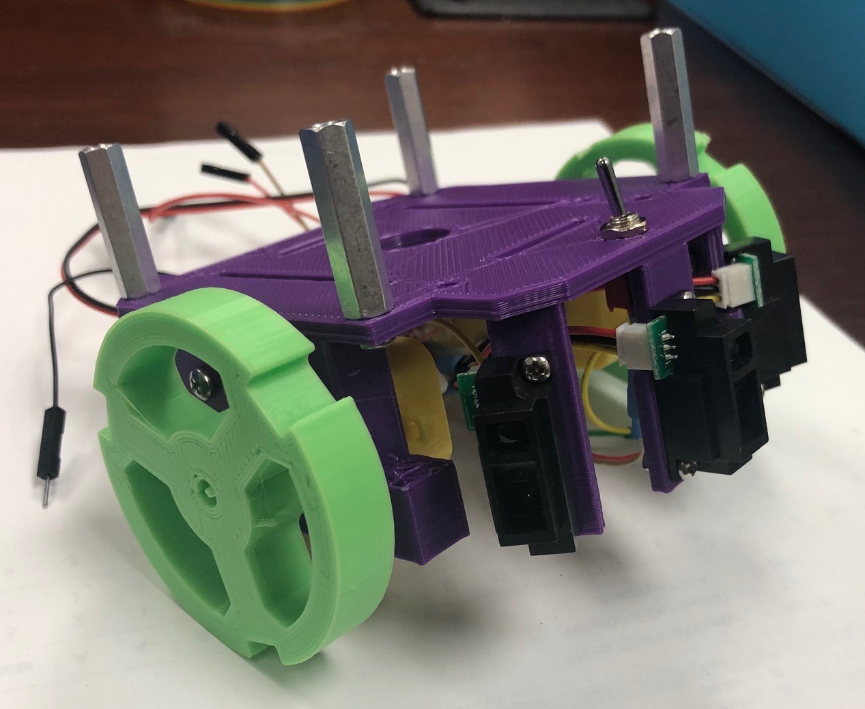
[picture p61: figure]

9. Battery: Connect a male to female jumper to the BATT headers on the PCB and feed through a slot in Layer B. These wires will connect to the battery and enable the removal of the battery without taking apart the bot.

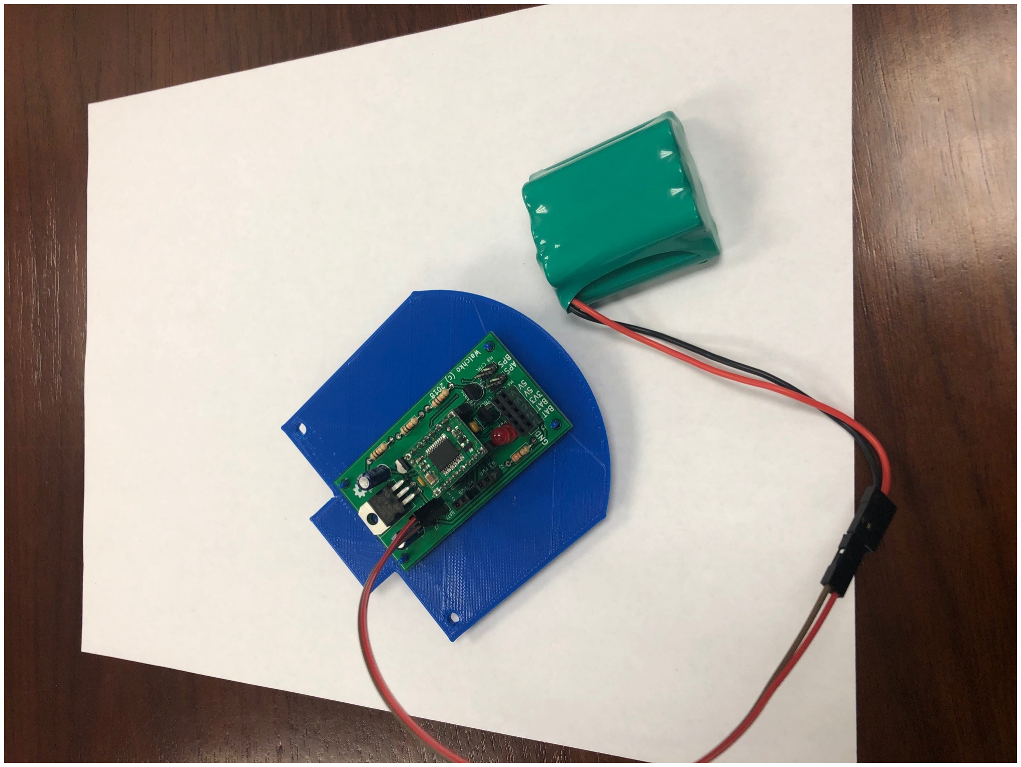
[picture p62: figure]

10. Testing PCB: Wire the motors, Arduino, battery, and switch to the PCB as shown in Figure. Download the robot_pcb folder from Teams (Labs/robot_pcb). Copy the Motor library from Teams (Labs/Custom Libraries/Motor) to your documents folder:
Documents/Arduino/libraries/ Open the robot_pcb.ino file. Compile and upload to the Arduino.

If working correctly, the tires should go forward for 1 second, then left for 1 second, then right for 1 second, then backwards for 1 second. Disconnect the PCB from the Arduino.

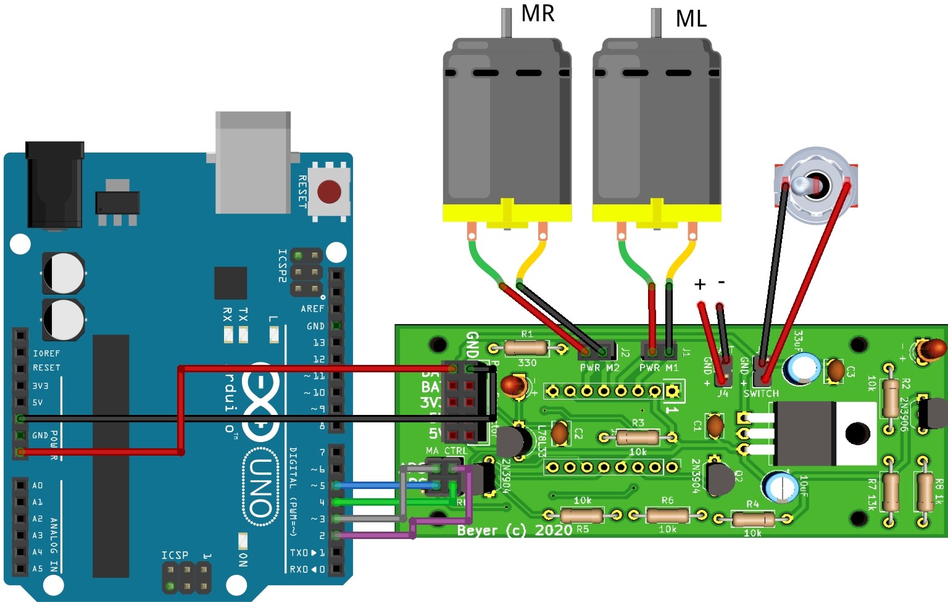
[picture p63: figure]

11. Secure the battery to Layer B using velcro.


5 Layer C - Arduino Layer.

1. Connect Layer C to Layer B using the larger standoffs.
2. Place the Arduino on the printed spacers (will only go one direction).
3. Wire the Arduino to the PCB going through the slots in Layer C and B.
4. Feed the wires from the IR sensors through the slots at the front of Layer B and C.


6 Connect Layer A to Layer B/C.

1. Connect the three layers using the line sensor mount and 2 - # 4-40 x 1” bolts and nuts.


2. Put the tires on the wheels.

7 Testing.


1. Connect the battery to the jumper and turn on the PCB. The robot should drive in the same pattern as before.

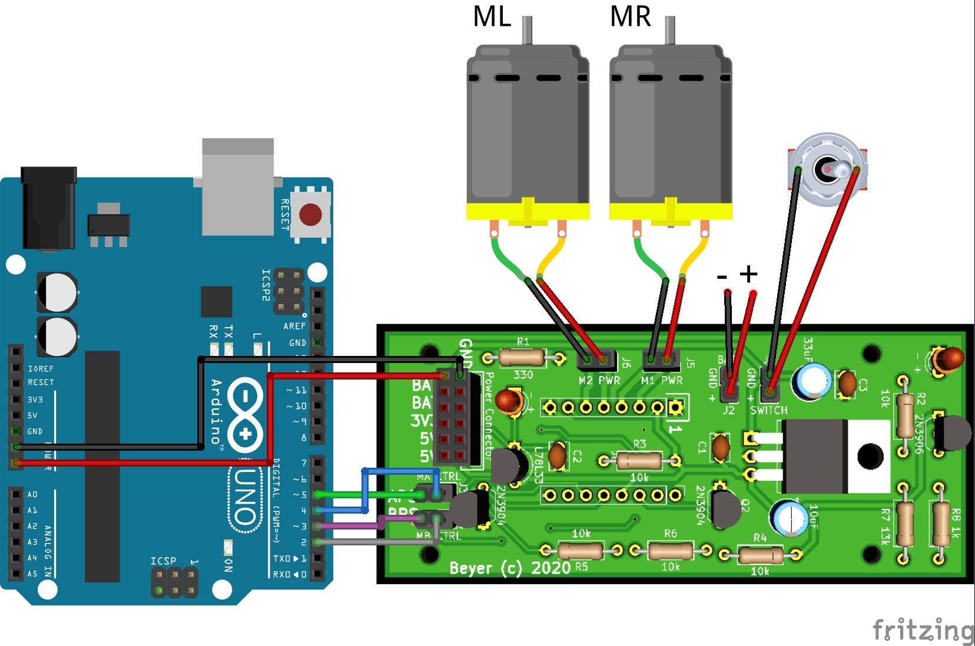
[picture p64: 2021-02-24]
Labs/1_robot_build/figs/6.jpg

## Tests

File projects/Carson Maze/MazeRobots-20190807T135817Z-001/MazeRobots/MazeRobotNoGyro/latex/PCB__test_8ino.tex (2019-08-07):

\hypertarget{PCB__test_8ino}{}\section{P\+C\+B\+\_\+test/\+P\+C\+B\+\_\+test/\+P\+C\+B\+\_\+test.ino File Reference}
\label{PCB__test_8ino}\index{P\+C\+B\+\_\+test/\+P\+C\+B\+\_\+test/\+P\+C\+B\+\_\+test.\+ino@{P\+C\+B\+\_\+test/\+P\+C\+B\+\_\+test/\+P\+C\+B\+\_\+test.\+ino}}

The main file for the project.  

{\ttfamily \#include \char`\"{}T\+B6612\+F\+N\+G.\+h\char`\"{}}\newline
{\ttfamily \#include \char`\"{}drive.\+h\char`\"{}}\newline
{\ttfamily \#include \char`\"{}I\+R.\+h\char`\"{}}\newline
{\ttfamily \#include \char`\"{}graph.\+h\char`\"{}}\newline
Include dependency graph for P\+C\+B\+\_\+test.\+ino\+:
\nopagebreak
\begin{figure}[H]
\begin{center}
\leavevmode

\end{center}
\end{figure}
\subsection*{Functions}
\begin{DoxyCompactItemize}
\item 
\mbox{\Hypertarget{PCB__test_8ino_ab7aece27431c153f5407864297b7c32b}\label{PCB__test_8ino_ab7aece27431c153f5407864297b7c32b}} 
void {\bfseries drive\+I\+R\+Adjust} (double spd)
\item 
\mbox{\Hypertarget{PCB__test_8ino_a56dfd95fece10fad4869ceb37cfe035d}\label{PCB__test_8ino_a56dfd95fece10fad4869ceb37cfe035d}} 
void {\bfseries drive\+Distance} (double mm)
\item 
\mbox{\Hypertarget{PCB__test_8ino_abe60ad2fecd7fb38997addbd92d88c68}\label{PCB__test_8ino_abe60ad2fecd7fb38997addbd92d88c68}} 
\hyperlink{util_8h_a92e22a126ad6bf9d255b517e70d083f6}{Direction} \hyperlink{PCB__test_8ino_abe60ad2fecd7fb38997addbd92d88c68}{next\+Move} ()
\begin{DoxyCompactList}\small\item\em Determines the next direction to be traveled in based on th Trémaux algorithm. s. \end{DoxyCompactList}\item 
\hyperlink{util_8h_a92e22a126ad6bf9d255b517e70d083f6}{Direction} \hyperlink{PCB__test_8ino_abc9fd4d649a1719e3e8f25cf3fd22857}{explore\+Edge} (long l\+Start, long r\+Start, bool need\+Acceleration)
\begin{DoxyCompactList}\small\item\em Moves the robot into the next cell, updates the cell, and readies the robot for its next action. \end{DoxyCompactList}\item 
\mbox{\Hypertarget{PCB__test_8ino_ad9d79fb25b7ad31450ea631b61f1883e}\label{PCB__test_8ino_ad9d79fb25b7ad31450ea631b61f1883e}} 
void \hyperlink{PCB__test_8ino_ad9d79fb25b7ad31450ea631b61f1883e}{wait\+For\+Power} ()
\begin{DoxyCompactList}\small\item\em Stops the robot\textquotesingle{}s movement and waits for the motor driver to be powered. \end{DoxyCompactList}\item 
\mbox{\Hypertarget{PCB__test_8ino_a4fc01d736fe50cf5b977f755b675f11d}\label{PCB__test_8ino_a4fc01d736fe50cf5b977f755b675f11d}} 
void {\bfseries setup} ()
\item 
\mbox{\Hypertarget{PCB__test_8ino_a25f18de883c5d893238db0b25fb9f471}\label{PCB__test_8ino_a25f18de883c5d893238db0b25fb9f471}} 
void {\bfseries update\+Cell} ()
\item 
int \hyperlink{PCB__test_8ino_a1f32d7057151c1c7f0f16a945a27af1e}{count\+Consecutive\+Turns} (\hyperlink{util_8h_a92e22a126ad6bf9d255b517e70d083f6}{Direction} next\+Dir)
\item 
\mbox{\Hypertarget{PCB__test_8ino_afe461d27b9c48d5921c00d521181f12f}\label{PCB__test_8ino_afe461d27b9c48d5921c00d521181f12f}} 
void {\bfseries loop} ()
\end{DoxyCompactItemize}
\subsection*{Variables}
\begin{DoxyCompactItemize}
\item 
\mbox{\Hypertarget{PCB__test_8ino_a1e70493ed842f246d8063b125681035b}\label{PCB__test_8ino_a1e70493ed842f246d8063b125681035b}} 
const double {\bfseries base\+\_\+speed} = 0.\+1
\item 
\mbox{\Hypertarget{PCB__test_8ino_ae30d704126646e0796e7ae5bf81cf672}\label{PCB__test_8ino_ae30d704126646e0796e7ae5bf81cf672}} 
const double {\bfseries bonus\+\_\+speed} = 0.\+25
\item 
\mbox{\Hypertarget{PCB__test_8ino_a3890cece9117b131b8bcb75369f4dfee}\label{PCB__test_8ino_a3890cece9117b131b8bcb75369f4dfee}} 
bool {\bfseries returning} = false
\item 
\mbox{\Hypertarget{PCB__test_8ino_a212e6b8f7e9ed2662711ad228dfc3e25}\label{PCB__test_8ino_a212e6b8f7e9ed2662711ad228dfc3e25}} 
\hyperlink{classRobot}{Robot} {\bfseries robot}
\item 
\mbox{\Hypertarget{PCB__test_8ino_a8c326d5209c586c6000e6759ade650b8}\label{PCB__test_8ino_a8c326d5209c586c6000e6759ade650b8}} 
\hyperlink{classIRSensor}{I\+R\+Sensor} {\bfseries l\+Sensor} (A0)
\item 
\mbox{\Hypertarget{PCB__test_8ino_a27bb774513555df6c77bc1887a8a0051}\label{PCB__test_8ino_a27bb774513555df6c77bc1887a8a0051}} 
\hyperlink{classIRSensor}{I\+R\+Sensor} {\bfseries m\+Sensor} (A1)
\item 
\mbox{\Hypertarget{PCB__test_8ino_a44d9f15f5aeb21ba1644f0841923675e}\label{PCB__test_8ino_a44d9f15f5aeb21ba1644f0841923675e}} 
\hyperlink{classIRSensor}{I\+R\+Sensor} {\bfseries r\+Sensor} (A2)
\item 
\mbox{\Hypertarget{PCB__test_8ino_a6a37c2944407d91bb5c144ca389b5392}\label{PCB__test_8ino_a6a37c2944407d91bb5c144ca389b5392}} 
bool {\bfseries accel} = true
\item 
\mbox{\Hypertarget{PCB__test_8ino_a4611dcb32e5240292b63bc6500226233}\label{PCB__test_8ino_a4611dcb32e5240292b63bc6500226233}} 
long {\bfseries last\+L\+Enc} = 0
\item 
\mbox{\Hypertarget{PCB__test_8ino_a79d7274f3f561f55ca0682ebfc0fb9b5}\label{PCB__test_8ino_a79d7274f3f561f55ca0682ebfc0fb9b5}} 
long {\bfseries last\+R\+Enc} = 0
\item 
\mbox{\Hypertarget{PCB__test_8ino_a9cc7ff928f7c1ebb843c1e3e22217430}\label{PCB__test_8ino_a9cc7ff928f7c1ebb843c1e3e22217430}} 
int {\bfseries turn\+Counter} = 0
\item 
\mbox{\Hypertarget{PCB__test_8ino_a4112c2be08cb7e9d80bc795fe94aa25c}\label{PCB__test_8ino_a4112c2be08cb7e9d80bc795fe94aa25c}} 
int {\bfseries turn\+Type} = 0
\end{DoxyCompactItemize}

\subsection{Detailed Description}
The main file for the project. 

This file contains the setup() and loop() functions, as well as a few functions related to advanced robot control and pathfinding. 

\subsection{Function Documentation}
\mbox{\Hypertarget{PCB__test_8ino_a1f32d7057151c1c7f0f16a945a27af1e}\label{PCB__test_8ino_a1f32d7057151c1c7f0f16a945a27af1e}} 
\index{P\+C\+B\+\_\+test.\+ino@{P\+C\+B\+\_\+test.\+ino}!count\+Consecutive\+Turns@{count\+Consecutive\+Turns}}
\index{count\+Consecutive\+Turns@{count\+Consecutive\+Turns}!P\+C\+B\+\_\+test.\+ino@{P\+C\+B\+\_\+test.\+ino}}
\subsubsection{\texorpdfstring{count\+Consecutive\+Turns()}{countConsecutiveTurns()}}
{\footnotesize\ttfamily int count\+Consecutive\+Turns (\begin{DoxyParamCaption}\item[{\hyperlink{util_8h_a92e22a126ad6bf9d255b517e70d083f6}{Direction}}]{next\+Dir }\end{DoxyParamCaption})}

Based on the next direction to go in and the current heading of the robot, determines what kind of turn must be taken and updates a counter.

\begin{DoxyReturn}{Returns}
The number of consecutive turns in the same direction taken so far 
\end{DoxyReturn}
\mbox{\Hypertarget{PCB__test_8ino_abc9fd4d649a1719e3e8f25cf3fd22857}\label{PCB__test_8ino_abc9fd4d649a1719e3e8f25cf3fd22857}} 
\index{P\+C\+B\+\_\+test.\+ino@{P\+C\+B\+\_\+test.\+ino}!explore\+Edge@{explore\+Edge}}
\index{explore\+Edge@{explore\+Edge}!P\+C\+B\+\_\+test.\+ino@{P\+C\+B\+\_\+test.\+ino}}
\subsubsection{\texorpdfstring{explore\+Edge()}{exploreEdge()}}
{\footnotesize\ttfamily \hyperlink{util_8h_a92e22a126ad6bf9d255b517e70d083f6}{Direction} explore\+Edge (\begin{DoxyParamCaption}\item[{long}]{l\+Start,  }\item[{long}]{r\+Start,  }\item[{bool}]{need\+Acceleration }\end{DoxyParamCaption})}

Moves the robot into the next cell, updates the cell, and readies the robot for its next action. 

This function moves the robot from the center of one cell to the edge of the cell it is currently facing. It then updates the new cell and decides which direction to go next, stopping or returning once the robot reaches the center of the new cell.

\begin{DoxyParams}{Parameters}
{\em l\+Start} & The starting value of the left encoder to be measured from \\
\hline
{\em r\+Start} & The starting value of the right encoder to be measured from \\
\hline
{\em need\+Acceleration} & \textquotesingle{}true\textquotesingle{} if the function is called from a dead stop, \textquotesingle{}false\textquotesingle{} if the function is called while the robot is already moving. \\
\hline
\end{DoxyParams}
\begin{DoxyReturn}{Returns}
The new direction for the robot to travel in as determined by the pathfinding algorithm. 
\end{DoxyReturn}

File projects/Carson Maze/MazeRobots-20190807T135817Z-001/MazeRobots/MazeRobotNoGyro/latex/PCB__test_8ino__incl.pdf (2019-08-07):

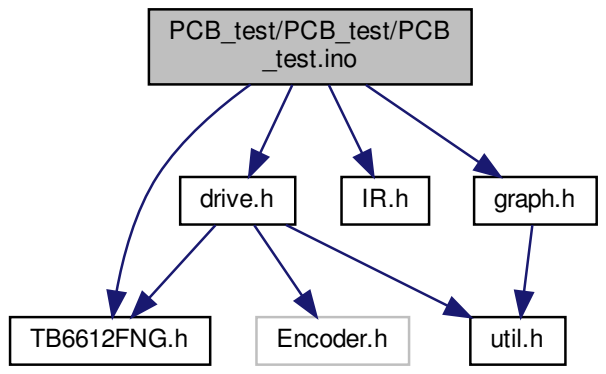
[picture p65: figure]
PCB_test/PCB_test/PCB _test.ino; TB6612FNG.h; drive.h; graph.h; Encoder.h; util.h

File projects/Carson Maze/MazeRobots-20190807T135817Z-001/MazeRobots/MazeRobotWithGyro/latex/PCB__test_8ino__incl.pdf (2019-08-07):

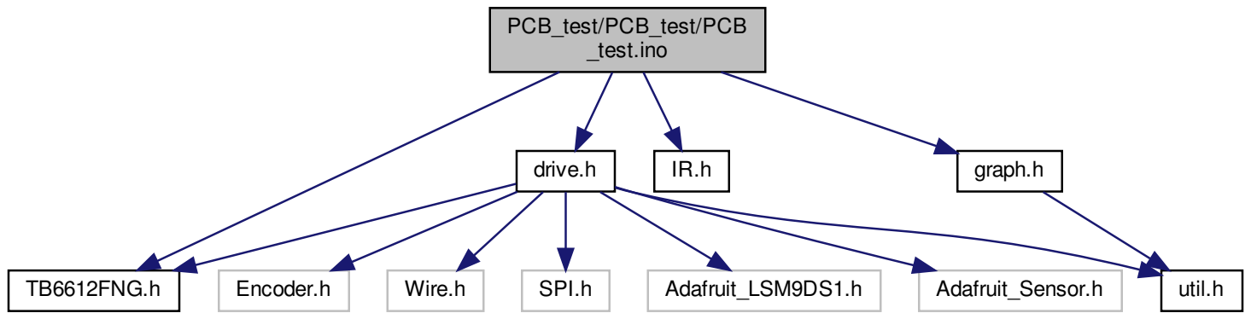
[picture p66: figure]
PCB_test/PCB_test/PCB _test.ino; TB6612FNG.h; drive.h; graph.h; Encoder.h; Wire.h; SPI.h; Adafruit_LSM9DS1.h; Adafruit_Sensor.h; util.h

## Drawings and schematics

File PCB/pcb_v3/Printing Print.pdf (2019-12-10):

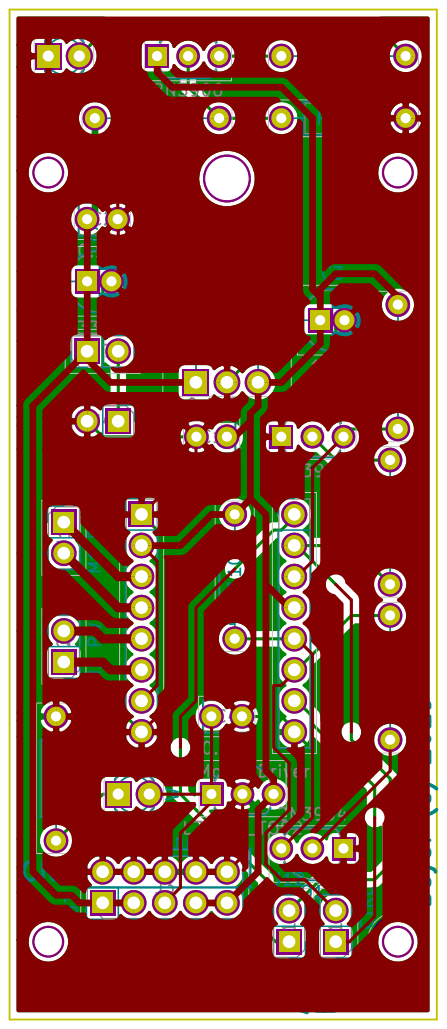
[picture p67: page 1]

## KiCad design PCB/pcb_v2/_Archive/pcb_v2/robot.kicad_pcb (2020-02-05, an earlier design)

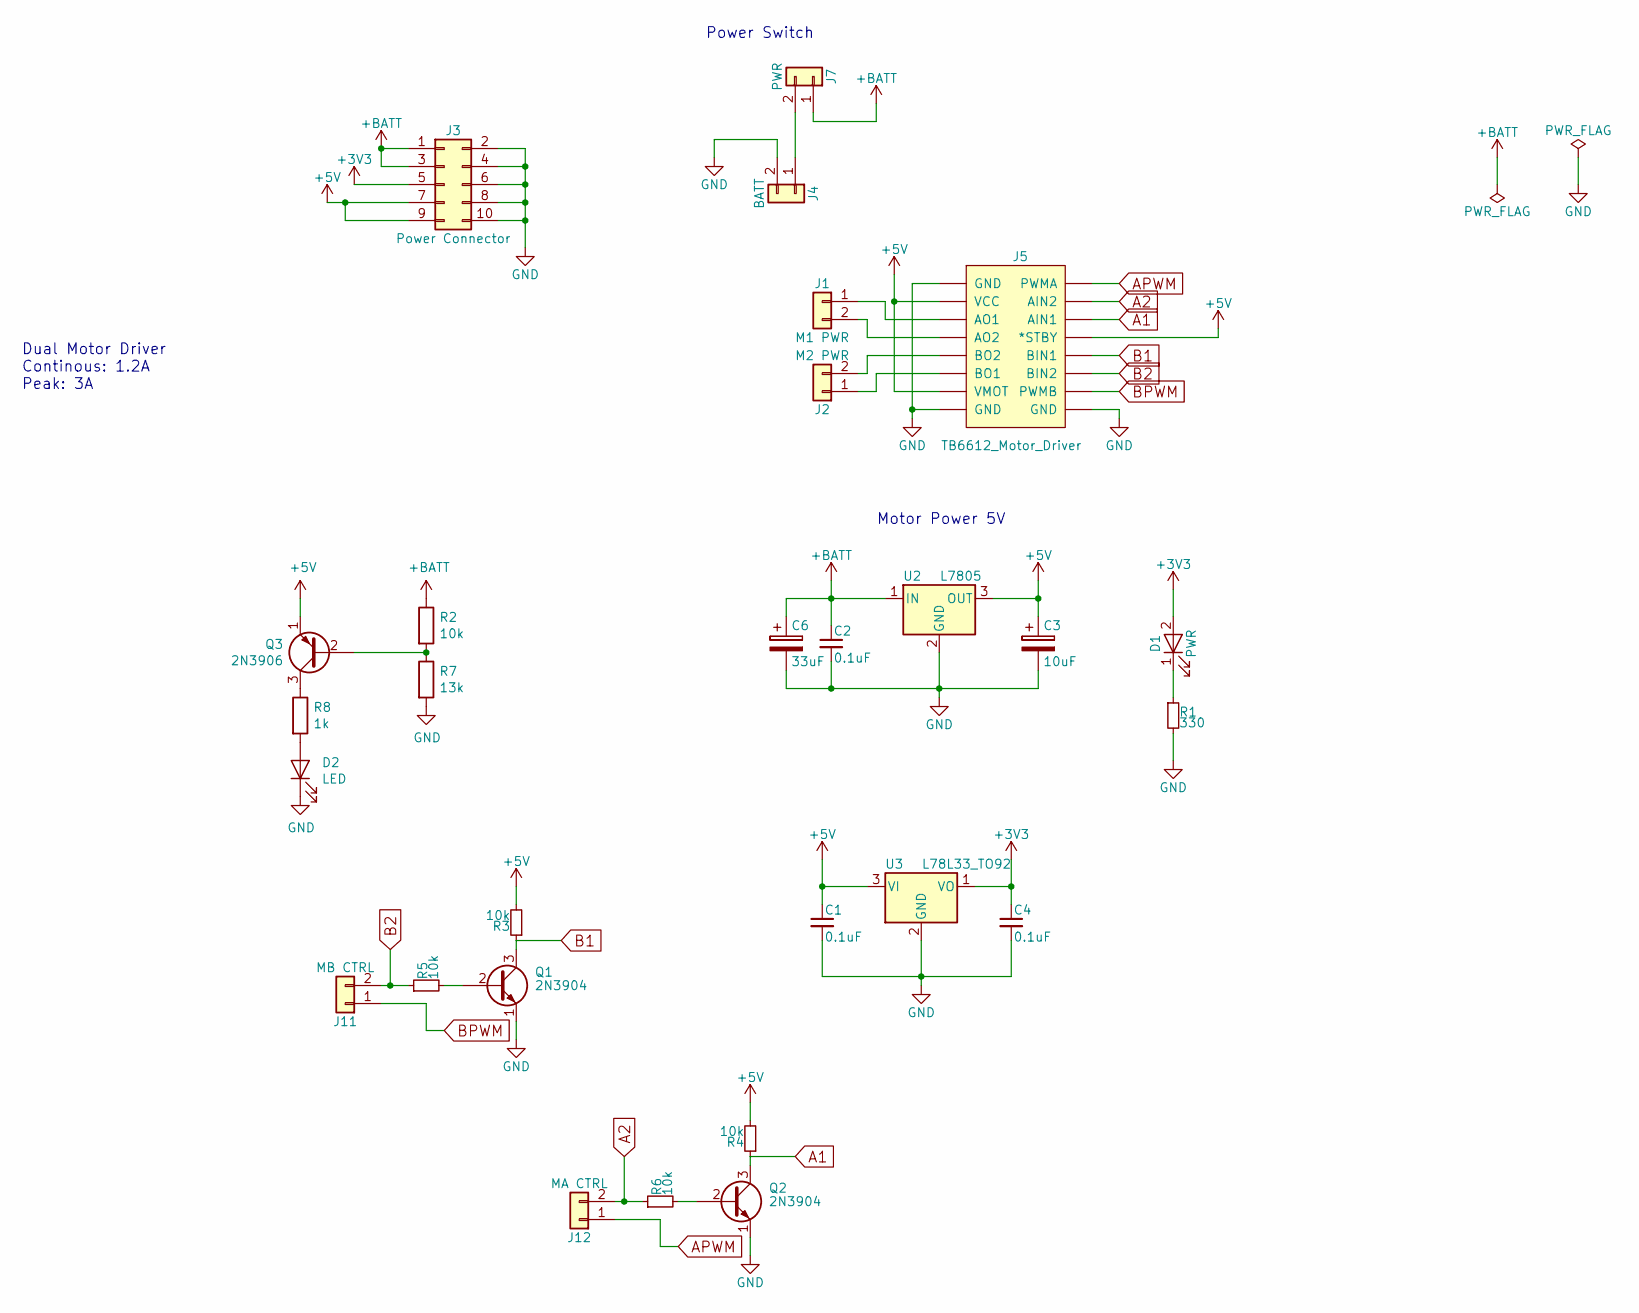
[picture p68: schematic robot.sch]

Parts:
C1, C2, C4: 0.1uF; C_Disc_D3.8mm_W2.6mm_P2.50mm
C3: 10uF; CP_Radial_D5.0mm_P2.00mm
C6: 33uF; CP_Radial_D5.0mm_P2.00mm
D1: PWR; LED_D3.0mm
D2: LED; LED_D3.0mm
J1: M1 PWR; Pin_Header_Straight_1x02_Pitch2.54mm
J2: M2 PWR; Pin_Header_Straight_1x02_Pitch2.54mm
J3: Power Connector; Pin_Header_Straight_2x05_Pitch2.54mm
J4: BATT; Pin_Header_Straight_1x02_Pitch2.54mm
J5: TB6612_Motor_Driver; Pololu_TB6612
J7: PWR; Pin_Header_Straight_1x02_Pitch2.54mm
J11: MB CTRL; Pin_Header_Straight_1x02_Pitch2.54mm
J12: MA CTRL; Pin_Header_Straight_1x02_Pitch2.54mm
Q1, Q2: 2N3904; TO-92L_Inline_Wide
Q3: 2N3906; TO-92_Inline_Wide
R1: 330; R_Axial_DIN0207_L6.3mm_D2.5mm_P10.16mm_Horizontal
R2, R3, R4, R5, R6: 10k; R_Axial_DIN0207_L6.3mm_D2.5mm_P10.16mm_Horizontal
R7: 13k; R_Axial_DIN0207_L6.3mm_D2.5mm_P10.16mm_Horizontal
R8: 1k; R_Axial_DIN0207_L6.3mm_D2.5mm_P10.16mm_Horizontal
U2: L7805; TO-220-3_Horizontal
U3: L78L33_TO92; TO-92L_Inline_Wide

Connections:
+3V3: C4.1, D1.2 (A), J3.5, U3.1 (VO)
+5V: C1.1, C3.1, J3.7, J3.9, J5.2 (VCC), J5.7 (VMOT), J5.13 (*STBY), Q3.1 (E), R3.2, R4.2, U2.3 (OUT), U3.3 (VI)
+BATT: C2.1, C6.1, J3.1, J3.3, J7.1, R2.1, U2.1 (IN)
A1: J5.14 (AIN1), Q2.3 (C), R4.1
A2: J5.15 (AIN2), J12.2, R6.1
APWM: J5.16 (PWMA), J12.1
B1: J5.12 (BIN1), Q1.3 (C), R3.1
B2: J5.11 (BIN2), J11.2, R5.1
BPWM: J5.10 (PWMB), J11.1
GND: C1.2, C2.2, C3.2, C4.2, C6.2, D2.1 (K), J3.2, J3.4, J3.6, J3.8, J3.10, J4.2, J5.1 (GND), J5.8 (GND), J5.9 (GND), Q1.1 (E), Q2.1 (E), R1.2, R7.2, U2.2 (GND), U3.2 (GND)
unnamed: D1.1 (K), R1.1
unnamed: D2.2 (A), R8.2
unnamed: J1.1, J5.3 (AO1)
unnamed: J1.2, J5.4 (AO2)
unnamed: J2.1, J5.6 (BO1)
unnamed: J2.2, J5.5 (BO2)
unnamed: J4.1, J7.2
unnamed: Q1.2 (B), R5.2
unnamed: Q2.2 (B), R6.2
unnamed: Q3.2 (B), R2.2, R7.1
unnamed: Q3.3 (C), R8.1

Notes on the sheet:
Power Switch
Motor Power 5V
Dual Motor Driver Continous: 1.2A Peak: 3A

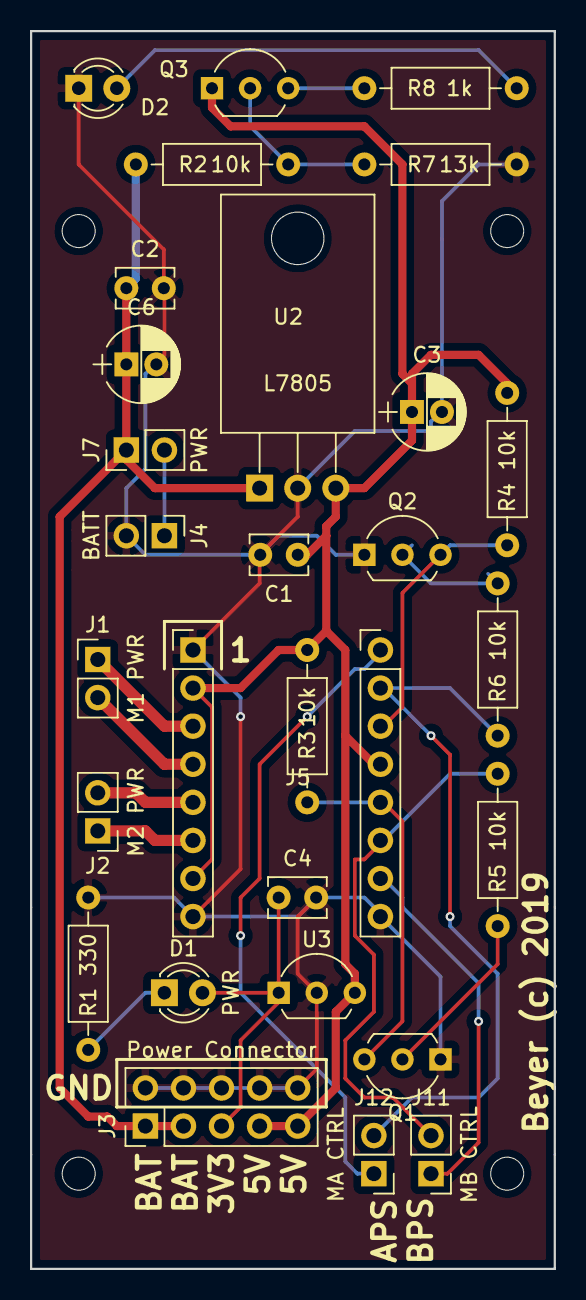
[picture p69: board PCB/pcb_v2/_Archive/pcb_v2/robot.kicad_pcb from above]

Board: 2 copper layers, 34.9 x 82.5 mm, 28 parts (0 on the bottom side), 21 nets.

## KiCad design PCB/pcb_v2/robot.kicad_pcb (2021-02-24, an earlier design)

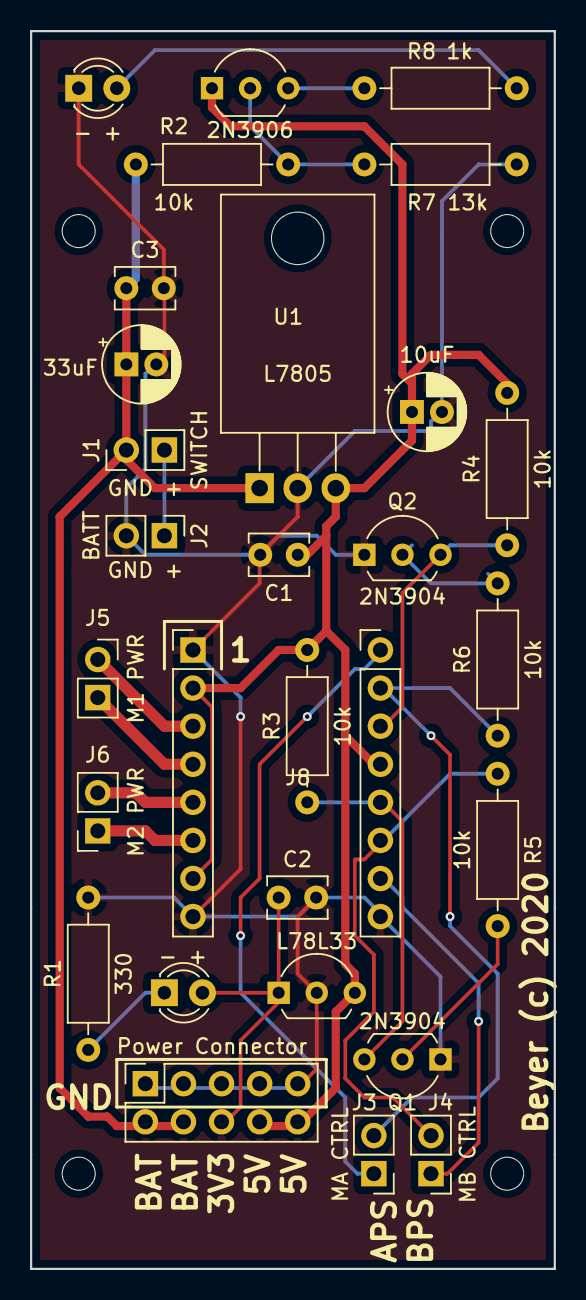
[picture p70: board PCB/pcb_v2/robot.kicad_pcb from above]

Board: 2 copper layers, 34.9 x 82.5 mm, 28 parts (0 on the bottom side), 18 nets.

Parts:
C1, C2, C3: 0.1uF; C_Disc_D3.8mm_W2.6mm_P2.50mm
C4: 10uF; CP_Radial_D5.0mm_P2.00mm
C5: 33uF; CP_Radial_D5.0mm_P2.00mm
D1, D2: - +; LED_D3.0mm
J1: SWITCH; PinHeader_1x02_P2.54mm_Vertical
J2: BATT; PinHeader_1x02_P2.54mm_Vertical
J3: MA CTRL; PinHeader_1x02_P2.54mm_Vertical
J4: MB CTRL; PinHeader_1x02_P2.54mm_Vertical
J5: M1 PWR; PinSocket_1x02_P2.54mm_Vertical
J6: M2 PWR; PinSocket_1x02_P2.54mm_Vertical
J7: Power Connector; PinSocket_2x05_P2.54mm_Vertical
J8: TB6612_Motor_Driver; Pololu_TB6612
Q1, Q2: 2N3904; TO-92L_Inline_Wide
Q3: 2N3906; TO-92_Inline_Wide
R1: 330; R_Axial_DIN0207_L6.3mm_D2.5mm_P10.16mm_Horizontal
R2, R3, R4, R5, R6: 10k; R_Axial_DIN0207_L6.3mm_D2.5mm_P10.16mm_Horizontal
R7: 13k; R_Axial_DIN0207_L6.3mm_D2.5mm_P10.16mm_Horizontal
R8: 1k; R_Axial_DIN0207_L6.3mm_D2.5mm_P10.16mm_Horizontal
U1: L7805; TO-220-3_Horizontal_TabDown
U2: L78L33; TO-92L_Inline_Wide

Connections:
+3V3: C2.1, D1.2, J7.5, U2.1
+5V: C1.1, C4.1, J7.7, J7.9, J8.2, J8.7, J8.13, Q3.1, R3.2, R4.2, U1.3, U2.3
+BATT: C3.1, C5.1, J1.1, J7.1, J7.3, U1.1
A1: J8.14, Q2.3, R4.1
A2: J3.2, J8.15, R6.1
APWM: J3.1, J8.16
B1: J8.12, Q1.3, R3.1
B2: J4.2, J8.11, R5.1
BPWM: J4.1, J8.10
GND: C1.2, C2.2, C3.2, C4.2, C5.2, D2.1, J2.2, J7.2, J7.4, J7.6, J7.8, J7.10, J8.1, J8.8, J8.9, Q1.1, Q2.1, R1.2, U1.2, U2.2
unnamed: D1.1, R1.1
unnamed: J1.2, J2.1
unnamed: J5.1, J8.3
unnamed: J5.2, J8.4
unnamed: J6.1, J8.6
unnamed: J6.2, J8.5
unnamed: Q1.2, R5.2
unnamed: Q2.2, R6.2

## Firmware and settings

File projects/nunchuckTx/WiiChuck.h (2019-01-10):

/*
 * Nunchuck -- Use a Wii Nunchuck
 * Tim Hirzel http://www.growdown.com
 * 
 notes on Wii Nunchuck Behavior.
 This library provides an improved derivation of rotation angles from the nunchuck accelerometer data.
 The biggest different over existing libraries (that I know of ) is the full 360 degrees of Roll data
 from teh combination of the x and z axis accelerometer data using the math library atan2. 

 It is accurate with 360 degrees of roll (rotation around axis coming out of the c button, the front of the wii),
 and about 180 degrees of pitch (rotation about the axis coming out of the side of the wii).  (read more below)

 In terms of mapping the wii position to angles, its important to note that while the Nunchuck
 sense Pitch, and Roll, it does not sense Yaw, or the compass direction.  This creates an important
 disparity where the nunchuck only works within one hemisphere.  At a result, when the pitch values are 
 less than about 10, and greater than about 170, the Roll data gets very unstable.  essentially, the roll
 data flips over 180 degrees very quickly.   To understand this property better, rotate the wii around the
 axis of the joystick.  You see the sensor data stays constant (with noise).  Because of this, it cant know
 the difference between arriving upside via 180 degree Roll, or 180 degree pitch.  It just assumes its always
 180 roll.


 * 
 * This file is an adaptation of the code by these authors:
 * Tod E. Kurt, http://todbot.com/blog/
 *
 * The Wii Nunchuck reading code is taken from Windmeadow Labs
 * http://www.windmeadow.com/node/42
 * 
 * Conversion to Arduino 1.0 by Danjovic
 * http://hotbit.blogspot.com 
 * 
 * Modified by Phillip Warner to use ints for the acceleration outputs
 *
 */

#ifndef WiiChuck_h
#define WiiChuck_h


#include "Arduino.h"
#include <Wire.h>
#include <math.h>


// these may need to be adjusted for each nunchuck for calibration
#define ZEROX 510  
#define ZEROY 490
#define ZEROZ 460
#define RADIUS 210  // probably pretty universal

#define DEFAULT_ZERO_JOY_X 124
#define DEFAULT_ZERO_JOY_Y 132



class WiiChuck {
    private:
        uint8_t cnt;
        uint8_t status[6];		// array to store wiichuck output
        uint8_t averageCounter;
        //int accelArray[3][AVERAGE_N];  // X,Y,Z
        int i;
        int total;
        uint8_t zeroJoyX;   // these are about where mine are
        uint8_t zeroJoyY; // use calibrateJoy when the stick is at zero to correct
        int lastJoyX;
        int lastJoyY;
        int angles[3];

        bool lastZ, lastC;


    public:

        uint8_t joyX;
        uint8_t joyY;
        bool buttonZ;
        bool buttonC;
        void begin() 
        {
            Wire.begin();
            cnt = 0;
            averageCounter = 0;
            // instead of the common 0x40 -> 0x00 initialization, we
            // use 0xF0 -> 0x55 followed by 0xFB -> 0x00.
            // this lets us use 3rd party nunchucks (like cheap $4 ebay ones)
            // while still letting us use official oness.
            // only side effect is that we no longer need to decode bytes in _nunchuk_decode_byte
            // see http://forum.arduino.cc/index.php?topic=45924#msg333160
            //  
            Wire.beginTransmission(0x52);	// device address
            Wire.write(0xF0);
            Wire.write(0x55);
            Wire.endTransmission();
            delay(1);
            Wire.beginTransmission(0x52);
            Wire.write(0xFB);
            Wire.write((uint8_t)0x00);

            Wire.endTransmission();
            update();            
            for (i = 0; i<3;i++) {
                angles[i] = 0;
            }
            zeroJoyX = DEFAULT_ZERO_JOY_X;
            zeroJoyY = DEFAULT_ZERO_JOY_Y;
        }


        void calibrateJoy() {
            zeroJoyX = joyX;
            zeroJoyY = joyY;
        }

        void update() {

            Wire.requestFrom (0x52, 6);	// request data from nunchuck
            while (Wire.available ()) {
                // receive byte as an integer
                status[cnt] = _nunchuk_decode_byte (Wire.read()); //
                cnt++;
            }
            if (cnt > 5) {
                lastZ = buttonZ;
                lastC = buttonC;
                lastJoyX = readJoyX();
                lastJoyY = readJoyY();
                //averageCounter ++;
                //if (averageCounter >= AVERAGE_N)
                //    averageCounter = 0;

                cnt = 0;
                joyX = (status[0]);
                joyY = (status[1]);
                for (i = 0; i < 3; i++) 
                    //accelArray[i][averageCounter] = ((int)status[i+2] << 2) + ((status[5] & (B00000011 << ((i+1)*2) ) >> ((i+1)*2))); 
                    angles[i] = (status[i+2] << 2) + ((status[5] & (B00000011 << ((i+1)*2) ) >> ((i+1)*2))); 

                //accelYArray[averageCounter] = ((int)status[3] << 2) + ((status[5] & B00110000) >> 4); 
                //accelZArray[averageCounter] = ((int)status[4] << 2) + ((status[5] & B11000000) >> 6); 

                buttonZ = !( status[5] & B00000001);
                buttonC = !((status[5] & B00000010) >> 1);
                _send_zero(); // send the request for next bytes

            }
        }


    // UNCOMMENT FOR DEBUGGING
    //byte * getStatus() {
    //    return status;
    //}

    int readAccelX() {
       // total = 0; // accelArray[xyz][averageCounter] * FAST_WEIGHT;
        return angles[0] - ZEROX;
    }
    int readAccelY() {
        // total = 0; // accelArray[xyz][averageCounter] * FAST_WEIGHT;
        return angles[1] - ZEROY;
    }
    int readAccelZ() {
        // total = 0; // accelArray[xyz][averageCounter] * FAST_WEIGHT;
        return angles[2] - ZEROZ;
    }

    bool zPressed() {
        return (buttonZ && ! lastZ);
    }
    bool cPressed() {
        return (buttonC && ! lastC);
    }

    // for using the joystick like a directional button
    bool rightJoy(int thresh=60) {
        return (readJoyX() > thresh and lastJoyX <= thresh);
    }

    // for using the joystick like a directional button
    bool leftJoy(int thresh=60) {
        return (readJoyX() < -thresh and lastJoyX >= -thresh);
    }


    int readJoyX() {
        return (int) joyX - zeroJoyX;
    }

    int readJoyY() {
        return (int)joyY - zeroJoyY;
    }


    // R, the radius, generally hovers around 210 (at least it does with mine)
   // int R() {
   //     return sqrt(readAccelX() * readAccelX() +readAccelY() * readAccelY() + readAccelZ() * readAccelZ());  
   // }


    // returns roll degrees
    int readRoll() {
        return (int)(atan2(float(readAccelX()),float(readAccelZ()))/ M_PI * 180.0);
    }

    // returns pitch in degrees
    int readPitch() {        
        return (int) (acos(float(readAccelY())/RADIUS)/ M_PI * 180.0);  // optionally swap 'RADIUS' for 'R()'
    }

    private:
        uint8_t _nunchuk_decode_byte (uint8_t x)
        {
            //decode is only necessary with certain initializations 
            //x = (x ^ 0x17) + 0x17;
            return x;
        }

        void _send_zero()
        {
            Wire.beginTransmission (0x52);	// transmit to device 0x52
            Wire.write ((uint8_t)0x00);		// sends one byte
            Wire.endTransmission ();	// stop transmitting
        }

};


#endif

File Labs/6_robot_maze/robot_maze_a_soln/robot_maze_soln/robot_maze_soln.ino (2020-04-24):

/* 
 *  Filename: robot_wallfollowing.ino
 *  Author: Capt Steven Beyer
 *  Created: 21 April 2020
 *  Description: Example Arduino Sketch that prints 
 *    values from the DFECBot's right IR Sensor.
 *  
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
 *  Assignment:
 *    1) Print the values from the DFECBot's center and 
 *      left GP2Y0A51SK0F Analog Distance Sensor to the serial 
 *      monitor.
 *    2) Use a ruler to confirm the accuracy of each distance 
 *      sensor - the sensor should be fairly accurate between 
 *      3 cm and 12 cm.
 *    3) Program the DFECBot to follow wall on right.
 *    4) Program the DFECBot to follow wall on left.
 *    5) Program the DFECBot to stay between two walls.
 *    Note: Remove all print statements/delays when running your wall following
 *  
 *  Required Files:
 *    Libraries : none
 *    Packages  : none
 *    Files     : Motor.h, SharpDistSensor.h
 */

#include <SharpDistSensor.h>
#include "Motor.h"
#include "Classifier.h"

/******************** Sensor variables *****************/
// Analog pins used by the sensors
const byte irR = A0;
const byte irC = A1;
const byte irL = A2;

// Window size of the median filter (odd number, 1 = no filtering)
const byte medianFilterWindowSize = 5;

// Create an object instance of the SharpDistSensor class for each sensor
SharpDistSensor sensorR(irR, medianFilterWindowSize);
SharpDistSensor sensorC(irC, medianFilterWindowSize);
SharpDistSensor sensorL(irL, medianFilterWindowSize);


/******************** Controller variables *****************/
#define OFFSET 25     // dist from IR sensor to center of robot in mm
#define DESIRED 100   // desired dist from wall
#define PWMNOMINAL 100
#define SWING 20
#define PWMMIN (PWMNOMINAL-SWING)
#define PWMMAX (PWMNOMINAL+SWING)

// Proportional gain constant
const int Kp = 3;
const int Kp2 = 2;


// choose between modes:
//  0 - follow wall on right
//  1 - follow wall on left
//  2 - follow walls on both sides
const int Mode = 0;

void setup() {
  // Initialize the motors
  Motor_Init();
  
  // Set parameters for each sensor
  sensorR.setModel(SharpDistSensor::GP2Y0A51SK0F_5V_DS);
  sensorC.setModel(SharpDistSensor::GP2Y0A51SK0F_5V_DS);
  sensorL.setModel(SharpDistSensor::GP2Y0A51SK0F_5V_DS);
}

int Turn = 0;
int NextState = 0;
int NextSquare = 1;
int Time = 0;
const int SQUARE_TIME = 160;
enum scenario next_state = Error;
int TurnTime = 0;
const int TURN = 160;

void loop() {
  int error, setPoint, pwmR, pwmL;
  enum scenario wall_state = Error;
  
  // Read distance (in mm) for each sensor
  int16_t distR = sensorR.getDist() + OFFSET;
  int16_t distC = sensorC.getDist() + OFFSET;
  int16_t distL = sensorL.getDist() + OFFSET;

  wall_state = Classify(distL, distC, distR);

  // Error state, pause
  if(wall_state == Error || wall_state == LeftTooClose || wall_state == RightTooClose || wall_state == CenterTooClose){
    Motor_Stop();
  }

  // semaphores: NextSquare - move to next square when true
  //             Turn - begin turn when true
  //             NextState - next state has been recorded when true
  
  // code to move to next square, obtain next state when halfway to
  // next square, and then set turn variables when in next square
  // if turn is about to occur
  if(NextSquare){
    
    // walls on both sides, so use proportional controller to stay in middle
    if((wall_state == Straight && next_state == Straight) || (wall_state == Blocked && next_state == Blocked)){
      if((distL > DESIRED) && (distR > DESIRED)){
        setPoint = (distL + distR)/2;
      }else{
        setPoint = DESIRED;
      }
      if(distL < distR){
        error = distL - setPoint;
      }else{
        error = setPoint - distR;
      }
      // Proportional controller
      pwmR = PWMNOMINAL+Kp*error;
      pwmL = PWMNOMINAL-Kp*error;
    
      // Bounds checking
      if(pwmR < PWMMIN) pwmR = PWMMIN;
      if(pwmR > PWMMAX) pwmR = PWMMAX;
      if(pwmL < PWMMIN) pwmL = PWMMIN;
      if(pwmL > PWMMAX) pwmL = PWMMAX;
    }
    
    // gap, so stick to wall
    else{
      if((wall_state == LeftJoint) || (wall_state == LeftTurn)){
        error = DESIRED - distR;
      }
      else if((wall_state == RightJoint) || (wall_state == RightTurn)){
        error = distL - DESIRED;
      }
      else{
        error = 0;
      }
      pwmR = PWMNOMINAL + Kp2*error;
      pwmL = PWMNOMINAL - Kp2*error;
      Motor_Forward(pwmL, pwmR);
    }
    
    // when halfway to next square, gather next state information
    if((Time >= SQUARE_TIME/2) && !NextState){
      next_state = wall_state;
      NextState = 1;
    }
    
    // when in next square, if turn, set turn variables
    // reset tachometer step counter for turn or next square math
    // distance = (change in steps*wheel circ)/(360 pulses per rotation)
    else if((Time >= SQUARE_TIME) && NextState){
      Time = 0;
      NextState = 0;
      // if a turn is available, determine if turn is necessary
      // currently not smart: turns in direction available with left
      // as first choice
      if(next_state == Blocked){
        TurnTime = 2*TURN;
        NextSquare = 0;
        Turn = 1;
      }
      else if(next_state == LeftTurn){
        TurnTime = TURN;
        NextSquare = 0;
        Turn = 1;
      }
      else if(next_state == RightTurn){
        TurnTime = TURN*3;
        NextSquare = 0;
        Turn = 1;
      }
      else if(next_state == TeeJoint){
        TurnTime = TURN*3;
        NextSquare = 0;
        Turn = 1;
      }
      else if(next_state == CrossRoad){
        TurnTime = TURN;
        NextSquare = 0;
        Turn = 1;
      }
      else if(next_state == LeftJoint){
        TurnTime = 0;
        NextSquare = 0;
        Turn = 1;
      }
      else if(next_state == RightJoint){
        TurnTime = 0;
        NextSquare = 0;
        Turn = 1;
      }
      // if no turn available move to next square
      else if(next_state == Straight){
        NextSquare = 1;
        Turn = 0;
      }
    }
  }
  // begin turn
  else if(Turn){
    Motor_Left(PWMNOMINAL, PWMNOMINAL);
    if(Time > TurnTime){
      Turn = 0;
      Motor_Stop();
      NextSquare = 1;
    }
  }
  Time++;
}

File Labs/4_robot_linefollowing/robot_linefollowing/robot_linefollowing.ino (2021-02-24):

/* 
 *  Filename: robot_linefollowing.ino
 *  Author: Capt Steven Beyer
 *  Created: 23 April 2020
 *  Description: Example Arduino Sketch that prints 
 *    values from the DFECBot's QTR-8RC line sensor array.
 *    
 *    The setup phase of this example calibrates the sensors for ten seconds and
 *    turns on the Arduino's LED (usually on pin 13) while calibration is going
 *    on. During this phase, you should expose each reflectance sensor to the
 *    lightest and darkest readings they will encounter. For example, if you are
 *    making a line follower, you should slide the sensors across the line during
 *    the calibration phase so that each sensor can get a reading of how dark the
 *    line is and how light the ground is.  Improper calibration will result in
 *    poor readings.
 *  
 *  Source: Adapted from QTRRCExample.ino and QTRSensors.h
 *    https://github.com/pololu/qtr-sensors-arduino
 *    
 *  Assignment:
 *    1) Use a ruler to confirm the accuracy of the line sensor 
 *    read function
 *    2) Program the DFECBot to follow a line
 *    Note: Remove all print statements/delays when running your line following
 *  
 *  Required Files:
 *    Libraries : none
 *    Packages  : none
 *    Files     : Motor.h, QTR-8RC.h
 */

#include "QTR-8RC.h"
#include "Motor.h"

/******************** Sensor variables *****************/
QTRSensors qtr;

const uint8_t SensorCount = 8;
uint16_t sensorValues[SensorCount];

/******************** Controller variables *****************/
#define PWMNOMINAL 100
#define SWING 20
#define PWMMIN (PWMNOMINAL-SWING)
#define PWMMAX (PWMNOMINAL+SWING)

// Proportional gain constant
const int Kp = 3;

void setup()
{
  Motor_Init();
  
  // configure the sensors
  qtr.setTypeRC();
  qtr.setSensorPins((const uint8_t[]){6, 7, 8, 9, 10, 11, 12, 13}, SensorCount);
  //qtr.setEmitterPin(5);

  delay(500);

  // During calibration 
  // 2.5 ms RC read timeout (default) * 10 reads per calibrate() call
  // = ~25 ms per calibrate() call.
  // Call calibrate() 400 times to make calibration take about 10 seconds.
  for (uint16_t i = 0; i < 400; i++)
  {
    qtr.calibrate();
  }

  // print the calibration minimum values measured when emitters were on
  Serial.begin(9600);
  for (uint8_t i = 0; i < SensorCount; i++)
  {
    Serial.print(qtr.calibrationOn.minimum[i]);
    Serial.print(' ');
  }
  Serial.println();

  // print the calibration maximum values measured when emitters were on
  for (uint8_t i = 0; i < SensorCount; i++)
  {
    Serial.print(qtr.calibrationOn.maximum[i]);
    Serial.print(' ');
  }
  Serial.println();
  Serial.println();
  delay(1000);
}

void loop()
{
  int pwmR, pwmL;
  
  // read calibrated sensor values and obtain a measure of the line position
  // with a position of 0.1 mm relative to the center of the line 
  // -33.2 mm to 33.2 mm
  int16_t position = qtr.readLineBlack(sensorValues);

  // print the sensor values as numbers from 0 to 1000, where 0 means maximum
  // reflectance and 1000 means minimum reflectance, followed by the line
  // position
  for (uint8_t i = 0; i < SensorCount; i++)
  {
    Serial.print(sensorValues[i]);
    Serial.print('\t');
  }
  Serial.println(position);

  delay(250);

  // Proportional controller


  // Bounds checking
  if(pwmR < PWMMIN) pwmR = PWMMIN;
  if(pwmR > PWMMAX) pwmR = PWMMAX;
  if(pwmL < PWMMIN) pwmL = PWMMIN;
  if(pwmL > PWMMAX) pwmL = PWMMAX;

  // Drive forward

}

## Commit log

2019-01-10 SMB, 10 Jan 19, First Commit.
    [ArduinoLayer.f3d, ArduinoLayer.stl, BaseLayer.f3d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]
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2019-01-17 SMB, 17 Jan 2019, Updated fusion files for new stacking order and changed gcode.
    [ArduinoLayer.f3d, ArduinoLayer.stl, DFEC-robot_Beyer.xlsx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]
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2019-02-05 SMB, 5 Feb 2019, Updated wire diagrams, added some basic code, and added code for servo.
    [robot.fzz]
2019-02-05 SMB, 5 Feb 19, Updated baselayer and pimount.
    [BaseLayer.stl, PiCamerMount.stl]
2019-02-05 SMB, 5 Feb 19, Updated Arduino and Motor Layers .
    [ArduinoLayer.stl, MotorLayer.stl]
2019-02-05 SMB, 5 Feb 19, Updated 3D print files and gcode.
    [ArduinoLayer.stl, Layer.stl]
2019-02-06 SMB, 6 Feb 2019, Added letters to 3d printed components.
    [ArduinoLayer.stl, BaseLayer.stl, Layer.stl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]
2019-02-06 SMB, 6 Feb 19, Updated robot_camera.ino code to reset camera and increase speed of right motor.
    [drive.h, nunchuckTx.ino, robot_camera.ino]
2019-02-08 SMB, 8 Feb 2019, Added nameplate.
    [ArduinoLayer.f3d, BaseLayer.f3d, Layer.f3d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]
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2019-02-25 SMB, 25 Feb 19, Added images to camera code.
    [robot_camera.fzz]
2019-02-25 SMB, 25 Feb 19, Created a basic schematic for robot wiring.
    [robot_basic.fzz]
2019-02-25 SMB, 25 Feb 19, Updated folders to be a bit more clear.
    [robot.fzz]
2019-02-28 SMB, 28 Feb 19, updated motor layer 3d model.
    [BaseLayerExtended.stl, MotorLayer.f3d, MotorLayer.stl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]
2019-02-28 SMB, 28 Feb 19, Updated basic circuit fritz.
    [robot_basic.fzz]
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2019-03-05 SMB, 5 Mar 19, Updated 3d printing files.
    [ArduinoLayer.f3d, BaseLayer.f3d, Layer.f3d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]
2019-03-06 SMB, 6 Mar 2019, Updated motorLayer 3d print and created PCB_test code for simple testing.
    [MotorLayer.f3d, MotorLayer.stl, Ninja_Flex_Tire - left.STL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]
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2019-03-07 SMB, 7 Mar 2019, added lab write ups to the repo.
    [robot_basic.fzz]
2019-03-07 SMB, 7 Mar 2019, Deleted and cleaned up some files.
    [robot_basic.fzz]
2019-03-08 SMB, 8 Mar 19, Completed line following lab.
    [line.fzz]
2019-03-13 SMB, 12 Mar 19, updated 3d printing files and ir sensor code.
    [ArduinoLayer.f3d, ArduinoLayer.stl, BaseLayer.f3d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]
2019-03-16 SMB, 16 Mar 19, Finished Obstacle Avoidance lap.
    [ir.fzz]
2019-03-16 SMB, 16 Mar 2019, Fixed some typos in line following/obstacle avoidance.
    [robot_linefollowing.ino]
2019-06-05 SMB, 5 Jun 19, updated motor layer. git push
    [MotorLayer1.stl, MotorLayer2.stl, MotorLayer3.stl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]
2019-06-05 SMB, 5 Jun 19, added Fusion file for MotorLayer v2.
    [MotorLayer.f3d, MotorLayer1.stl, MotorLayer2.stl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]
2019-06-10 SMB, 10 Jun 19, Updated 3d print for base.
    [DFEC-robot_Beyer.xlsx]
2019-08-07 SMB, 7 Aug 19, Updated 3d print files and included tachometer version of BeyerBot within Carson folder.
    [ArduinoLayer.stl, BaseLayer.stl, Layer.stl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]
2019-08-29 Updated 3d print models for version 2.
    [ArduinoLayer.f3d, ArduinoLayer.stl, BaseLayer.f3d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]
2019-09-16 SMB, 16 Sep 19, Updated prints.
    [ArduinoLayer.f3d, ArduinoLayer.stl, robot-2019-07-11-12-28-16.sch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]
2019-12-10 SMB, 10 Dec 19, updated 3d print files.
    [BaseLayer.stl, DFEC-robot_Beyer.xlsx, MotorLayer.stl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]
2019-12-10 SMB, 10 Dec 19, Updated 3D Print for 8 Line Sensor Array. Updated drive code to create Motor.h allowing for individual control of motors. Closer code to TI Bot.
    [LineSensorHolder2.stl, line.fzz, robot_basic.fzz]
2019-12-16 SMB, 16 Dec 19, Updated solution code for line following to use a proportional controller.
    [ArduinoLayer2.stl, BaseLayer2.stl, Layer2.stl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]
2019-12-16 SMB, 16 Dec 19, updated obstacle avoidance solution to create a porportional controller that drives straight down the middle of two walls using filtered IR sensor values.
    [ir.fzz]
2020-02-05 Updated PCB files and some code.
    [robot-2020-01-31-07-03-44.sch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]
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2020-02-13 SMB, 13 Feb 2020, Updated STL for Base Layer for smaller standoffs.
    [BaseLayer2.stl]
2020-02-13 SMB, 13 Feb 2020, Updated stl and gcode for all of the prints.
    [ArduinoLayer.f3d, ArduinoLayer.stl, ArduinoLayer2.stl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]
2020-02-13 SMB, 13 Feb 2020, updated BaseLayer fusion code.
    [BaseLayer.f3d]
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2020-04-17 SMB, 17 Apr 2020, Updated code for Motor.h and labs 0, 1, 2, 3.
    [robot_basic.fzz]
2020-04-17 SMB, 17 Apr 2020, Updated file names.
    [robot_basic.fzz]
2020-04-22 SMB, 22 Apr 2020, updated wall following code.
    [ir.fzz, line.fzz, robot_basic.fzz]
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2020-04-24 SMB, 24 Apr 2020, Added code to complete the maze.
    [nunchuck_rcv.fzz, nunchuck_tx.fzz, robot-2019-07-11-12-28-16.sch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]
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2020-04-28 Printed ne pics for pcb_v2
    [robot.kicad_pcb]
2020-04-28 SMB, 28 Apr 2020, Updated PCB v2.
    [robot-B_Cu.gbl, robot-B_Cu.gbr, robot-B_Mask.gbr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]
2020-04-28 SMB, 28 Apr 2020, Created PCBv3.
    [robot-2019-07-11-12-28-16.sch, robot-2019-09-04-11-15-19.sch, robot-2020-01-31-07-03-44.sch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]
2020-04-28 SMB, 28 Apr 2020, Updated with PCB.
    [robot-2019-07-11-12-28-16.sch, robot-2019-09-04-11-15-19.sch, robot-2020-01-31-07-03-44.sch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]
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2020-04-28 SMB, 28 Apr 2020, fixed error in PCB.
    [robot-B_Cu.gbl, robot-B_Cu.gbr, robot-B_Mask.gbr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]
2020-04-29 SMB, got pictures ready for Lab 0.
    [robot_basic.fzz]
2020-04-29 SMB, 29 Apr 2020, Created v3 of 3d models.
    [ArduinoLayer.f3d, ArduinoLayer.stl, BaseLayer.f3d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]
2020-04-29 SMB, 29 Apr 2020, Updated a few things in PCB .
    [robot.sch]
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2020-04-29 SMB, 29 Apr 2020, Updated gerbers for PCB.
    [robot-B_Cu.gbl, robot-B_Cu.gbr, robot-B_Mask.gbr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]
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2020-09-02 SMB, 2 Sep 2020, fixed some issues where figures and folders in lab disappeared.
    [ir.fzz, line.fzz, robot_basic.fzz]
2020-09-02 SMB, 2 Sept 2020, Fixed error in Robot PCB'
2021-02-24 SMB, 24 Feb 2021, updated wiring schematic for PCB.
    [Body26.stl, Body27.stl, Body43.stl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]
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2021-06-30 Updates parts inventory and parts needed for AY2021-2022
    [ECE210_BeyerBot_2020-2021.xlsx]
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

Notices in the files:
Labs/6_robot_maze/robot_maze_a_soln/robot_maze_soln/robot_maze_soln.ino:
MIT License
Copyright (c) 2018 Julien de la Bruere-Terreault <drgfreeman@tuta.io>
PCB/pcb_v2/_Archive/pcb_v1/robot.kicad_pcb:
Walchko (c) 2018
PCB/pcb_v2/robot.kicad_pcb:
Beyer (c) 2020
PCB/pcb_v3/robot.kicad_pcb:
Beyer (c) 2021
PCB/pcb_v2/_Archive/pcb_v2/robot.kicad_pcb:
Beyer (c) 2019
